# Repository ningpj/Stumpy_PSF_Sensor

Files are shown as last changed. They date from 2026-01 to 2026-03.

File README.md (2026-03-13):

# "_Stumpy_" Proportional Sync-Feedback (PSF) Sensor Enclosure for Multi Material Printing

During extended periods of synchronised printing without intervening tool changes, alignment between extruder and gear steppers can gradually drift. Even with precise calibration, factors such as under extrusion during purging, printing at high speed near upper flow limits, friction and drag and the inertia of heavy spools can conspire to cause slippage in either the extruder or more commonly—the downstream gear stepper. Over time, this mismatch accumulates and can lead to print artefacts caused by missed steps or suboptimal extrusion rates. Although not always apparent on well-tuned systems, it's a legitimate and demonstrable issue.

Proportional sync-feedback sensors address this using linear Hall Effect sensors (or similar), providing real-time analog positional telemetry to Happy-Hare allowing it to continuously adjust and fine tune the following gear stepper's Rotational Distance (`RD`).

This enclosure has been based around the excellent `PSF v1.0 / 1.1` Proportional Sync-Feedback sensor kit from [**Kashine6**](https://github.com/kashine6/Proportional-Sync-Feedback-Sensor?tab=readme-ov-file) (Discord: @jacksky6) and is intended to be used with the **Happy-Hare** MMU ecosystem and new Flowguard / Sync-feedback controller facilities (Happy-Hare `3.4.2` or later). `14.5 mm` of buffer range and works with `20 mm` or `25 mm` compression springs from the kit (`20 mm` preferred).

## References & Acknowledgements

This design has been completely reworked from the ground up, incorporating improvements informed by field testing of MK I and the earlier adaptation of [Tshine's original dual micro-switch based Sync-feedback Sensor](https://makerworld.com/en/models/507573) by [Kashine6](https://github.com/kashine6/Proportional-Sync-Feedback-Sensor?tab=readme-ov-file) to support Proportional Sync-Feedback sensors.

The primary goals have been to further reduce the overall form factor, optimise sensor–magnet alignment and constrain shuttle lateral movement to maximise Hall Affect ADC signal fidelity, particularly for top‑mounted MMUs and central Bowden entry ports. The assembly now measures just `63 mm` in length — `9.2 mm` shorter than Kashine6’s version and `3 mm` shorter than MK I revision. The `ECAS04` captive retention design has also been refined to make it easier to install them, hopefully without splitting the base. Printable `ECAS04` clips have also been included to colour coordinate ;-)  

## Assembly

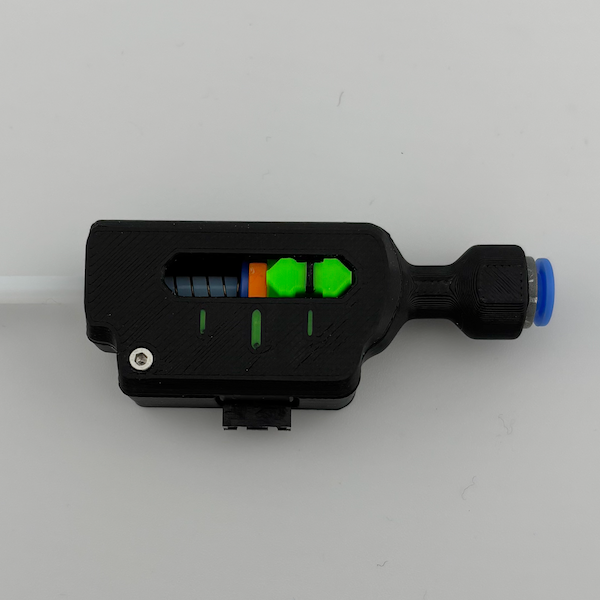
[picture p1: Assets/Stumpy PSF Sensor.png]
Stumpy PSF Sensor


> [!NOTE] 
> Step files (rather than STLs) are included for printing the sensor with [Multi-colour](MK%20II%20(Full%20redesign)/Multi_Colour_Step) tick marks or [Single-colour](MK%20II%20(Full%20redesign)/Single_Colour_Step) with recessed tick marks. Also consider lowering your 1st layer speed as the coloured elements are reasonably narrow to ensure tick marks are crisp and clean. 
> Depending on MMU / printer orientation, you may also consider inverting all parts (mirror along x axis in your slicer) to relocate the connector to the bottom of the unit to optimise wiring for your particular mmu setup.

Assembly is reasonably straight forward:

- Straighten the end of the PTFE tube you plan to use between the MMU and “Stumpy” PSF sensor. Avoid using PTFE with an `ID = 3.0 mm`. It klinks too easily especially if it needs to bend to accomodate the full range of gates / lanes which will jam the shuttle rather than moving freely for all selected gates.
- Check the body `4 mm` PTFE path with the PTFE tube to make sure its smooth and doesn't bind. Use a 4mm drill to gently remove any residual print artefacts around the 4 mm - 2 mm step down chamfer - Be careful not to damage the chamfer though.
- Install the `ECAS04` fittings without the optional rubber boot. You still need the hard plastic clasp cover on the base though.
- Press the `D4 × 15 mm` magnet into the PSF shuttle until it sits flush with the end opposite the `ECAS04` fitting. Magnet orientation doesn’t matter; Happy-Hare will calibrate it.
- Insert the  `2.0 – 2.5 mm ID` PTFE feeder tube from the left, feeding it through the `20 mm` spring (or `25 mm` if this is all you have) and shuttle until it bottoms out in the body recess. Adjust so it neither binds nor pulls out when held against the opposite stop. Install the colour coordinated `ECAS04` clip with the 90° top facing the shuttle so it’s retained and prevented from rotating by the nubs provided.
- Insert the `PSF 1.0 / v1.1` PCB module into the provided slot.
- Slide the lid / cover on from the back over the shuttle and onto the base, aligning the parts and snapping them gently onto the locating nubs. Do not force it. Secure with a single `M2 × 6 mm SHCS`.
- Confirm the shuttle moves freely across its full travel before installing.

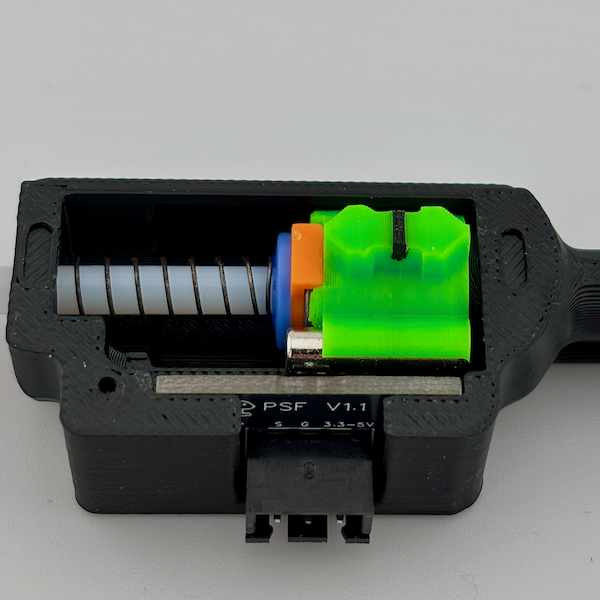
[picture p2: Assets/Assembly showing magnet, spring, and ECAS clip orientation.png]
Assembly showing magnet ECSA clip positions


## Bill of Materials (BOM)

| Item | Specification | Quantity |
| --- | --- | --- |
| **PSF v1.0/1.1+ Board** | Inexpensive kit from [Aliexpress](https://www.aliexpress.com/item/1005010470743517.html) that includes all the required parts below | 1 |
| **Spring** | 0.4 mm × 6 mm × 20 mm, spring steel ( If longer, e,g 25mm, cut down and shorten it, tiding up the cut end with needle nose pliers | 1 |
| **Magnet** | D4 mm × 15 mm N35 | 1 |
| **ECAS04 Bowden connector & clips**| | 2 |
| **M2×6 mm SHCS screw** | | 1 |
| **PTFE feeder tube** | Short PTFE feeder tube installed between the “Stumpy” PSF Sensor and the MMU (2.5 mm ID recommended) - 3 mm ID PTFE tube is too flexible and will deform or jam if its bent too much. | |

## Prerequsites

"Stumpy" PSF needs to be used inconjunction with `Happy-Hare` Flowguard **integrated** support for Proportional Feedback Sensors (Release `3.4.2` or later). Please refer to https://github.com/moggieuk/Happy-Hare/wiki/Synchronized-Gear-Extruder2 for proportional sensor setup, configuration, and usage instructions.

## Happy-Hare Configuration

`MMU_PARAMETERS.CFG`

The "Stumpy" PSF Sync-Feedback Sensor has 14.5mm of buffer / sensor range.

```yaml
sync_feedback_buffer_range: 14.5 		# Travel in "buffer" between compression/tension or one sensor and end (see above)
sync_feedback_buffer_maxrange: 14.5 	# Absolute maximum end-to-end travel (mm) provided by buffer (see above)
```

In `MMU_HARDWARE.CFG` set `sync_feedback_analog_pin: mmu:<ADC GPIO>` to a valid analog-capable GPIO port on the MCU you connected the "Stumpy" PSF sensor to. If `sync_feedback_*` parameters aren't defined under your `[mmu_sensor]` section, insert the following block manually, setting `compression`, `tension`, and `neutral_point` to 1, 0, & 0.5 respectively. 

[Kashine6](https://github.com/kashine6/Proportional-Sync-Feedback-Sensor?tab=readme-ov-file) provides a breakdown on their GITHUB of valid ADC GPIO ports for many popular MMU MCU's.  Note that while many boards offer multiple ADC-capable GPIO's, only one port has been fully verified and documented for each board.

Restart Klipper, load a gate with filament and run `MMU_CALIBRATE_PSENSOR` to determine the minimum and maximum ADC values returned by your PSF v1.0 / v1.1 Sensor module. Use these values to configure the corresponding parameters in `MMU_HARDWARE.CFG`. Your sensor may produce different or inverted—readings compared to the example below. This is expected, and Happy-Hare can accommodate it.

```yaml
sync_feedback_analog_pin: mmu:<Your analog-capable GPIO> # The ADC pin where the proportional filament pressure sensor is installed
sync_feedback_analog_max_compression: 0.9964             # Raw sensor reading at max filament compression (buffer squeezed)
sync_feedback_analog_max_tension: 0.0046                 # Raw sensor reading at max filament tension (buffer expanded)
sync_feedback_analog_neutral_point: 0.5005               # Sensor neutral point (tunable to apply positive tension on the filament to unburden the Bowden and extruder)
```

## Installation Options

Normal orientation with connector on top for right hand installation. Optionally mirror parts along x axis in your slicer to relocate the connector to the bottom of the unit to optimise wiring / visibility for your particular mmu setup.

For setups with a central PTFE entry port like mine, consider installing a PTFE guide as shown below to help straighten the PTFE path and ensure the sensor shuttle moves freely no matter the gate selected [Makerworld: HamAndChris 90°, 180°, or 60° PTFE Bowden tube bend guide](https://makerworld.com/en/models/1033408-90deg-180deg-or-60deg-ptfe-bowden-tube-bend-guide#profileId-1016713).

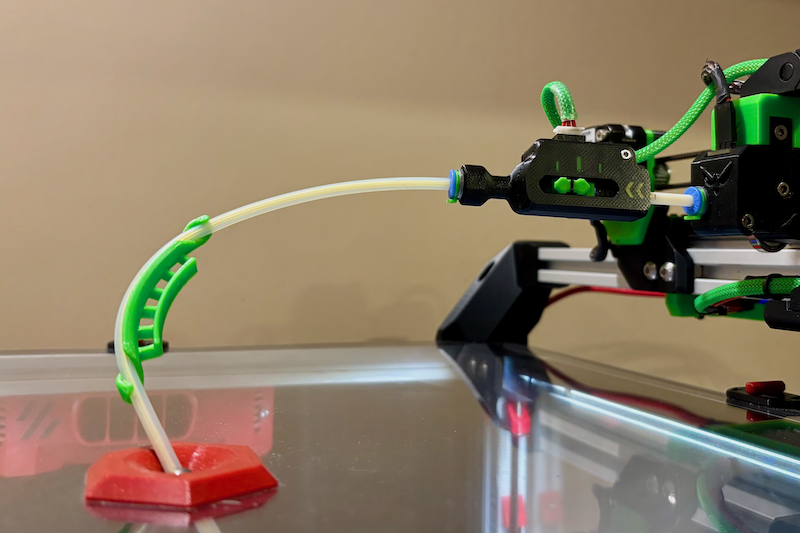
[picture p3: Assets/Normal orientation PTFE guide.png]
Normal Orientation, wired from top with PTFE guide
 

## Optional Shuttle with 3x2mm Magnet Stack

This variant is intended for people who want to self‑source / build the PSF sensor and have difficulty obtaining the preferred D4×15 mm magnet. Instead, it uses a stack of commonly available 3×2-ish mm N35 magnets. Depending on their thickness, the carrier will accept a stack of 7–9 magnets. When installing the shuttle ECAS, take care not to crack or deform the carrier.

Because magnetic flux varies, you may need to adjust the stack height or shift its position slightly to achieve saturation of the Hall‑effect sensor at both travel extremes. This tuning step is optional—the sensor will still function reliably without it. In testing, for example, saturation was achieved with eight magnets and the stack offset approximately 1.5 mm from the right side of the shuttle.

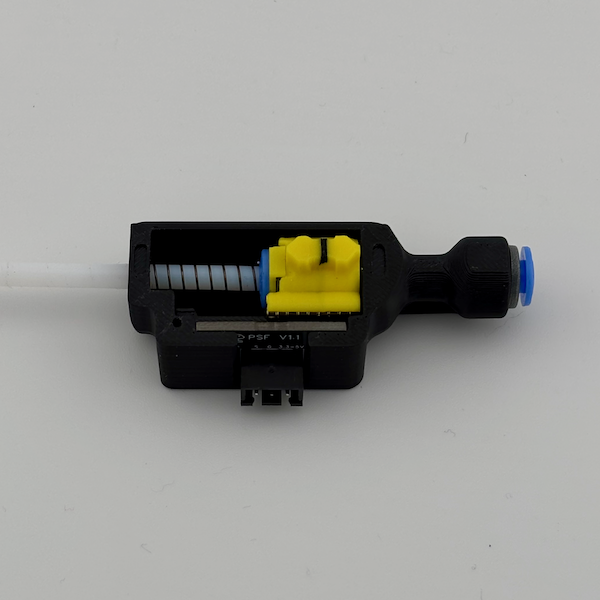
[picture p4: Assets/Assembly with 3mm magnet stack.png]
Optional 3x2mm Magnet Stack

<br>
<br>
With the slightly offset 3x2mm magnet stack (8), excellent `MMU_CALIBRATE_PSENSOR` results were achieved by repeatly adjusting the position / number of magnets and rerunning `MMU_CALIBRATE_PSENSOR` to confirm results.  

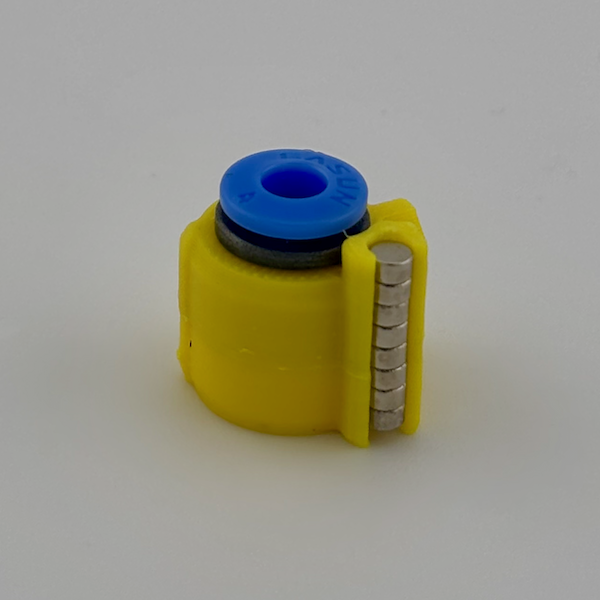
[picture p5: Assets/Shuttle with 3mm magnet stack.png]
Optimal 3x2mm Magnet offset


```yaml
// sync_feedback_analog_max_compression: 0.9809
// sync_feedback_analog_max_tension:     0.0043
// sync_feedback_analog_neutral_point:   0.4926
```

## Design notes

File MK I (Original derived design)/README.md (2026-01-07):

# *"Stumpy"* Proprotional Sync-Feedback (PSF) Sensor for Multi Material Printing

During extended periods of synchronised printing without intervening tool changes, alignment between extruder and gear steppers can gradually drift. Even with precise calibration, factors such as under extrusion during purging, printing at high speed near upper flow limits, friction and drag and the inertia of heavy spools can conspire to cause slippage in either the extruder or more commonly—the downstream gear stepper. Over time, this mismatch accumulates and can lead to print artefacts caused by missed steps or suboptimal extrusion rates. Although not always apparent on well-tuned systems, it's a legitimate and demonstrable issue.

Proportional sync-feedback sensors address this using linear Hall Effect sensors (or similar), providing analog positional telemetry to Happy Hare allowing it to continuously adjust and fine tune gear stepper Rotational Distance (RD).

This redesign is based around the PSF v1.0/1.1 or later proportional sensor kit from **Kashine6** on ALiexpress and is intended to be used with the **Happy Hare** MMU ecosystem and new Flowguard / Sync-feedback controller.

## References & Acknowledgements

This design is based on the original works of [Tshine's Dual Micro-switch based Sync-feedback Sensor](https://makerworld.com/en/models/507573) and subsequent adaption to accomodate Proportional Sync-Feedback (PSF) sensor circuitry and magnet by [Kashine6](https://github.com/kashine6/Proportional-Sync-Feedback-Sensor?tab=readme-ov-file). Its been optimised (sensor / magnet placement, mainbody changes, etc) and significantly shortened (65mm - 6.2mm shorter than Kashine6's version) to work better with top mounted MMU's and bowden entry ports.

## Assembly

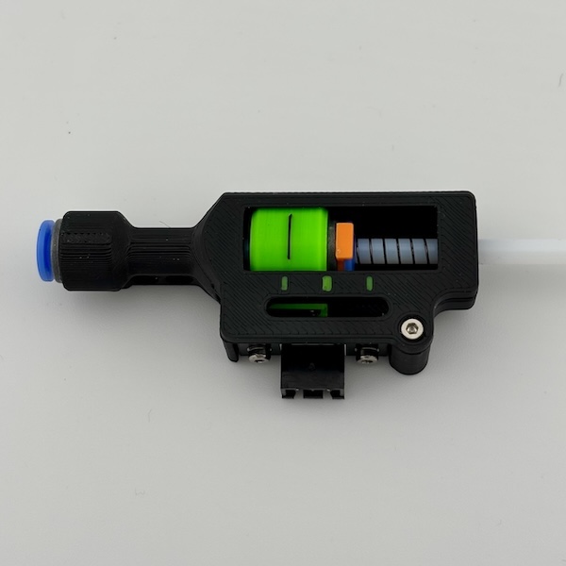
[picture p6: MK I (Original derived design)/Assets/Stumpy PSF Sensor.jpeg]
Stumpy PSF Sensor


> [!NOTE] 
> Step files (rather than STLs) are included for printing the sensor with [Multi-colour](Multi_Colour_Step) tick marks or  [Single-colour](Single_Colour_Step) with recessed tick marks.
> Depending on MMU / Printer orientation, you may elect to invert all the parts (mirror along x axis in your slicer) to move the connector to the top to streamline wiring. 

Assembly is reasonably straight forward.

- Install ECAS fittings without rubber boots
- Install D4 x 15mm magnet in PSF shuttle until it's flush with the end of the shuttle (magnetic orientation doesn't matter)
- Straighten the PTFE tube you will be inserting into the "Stumpy" PSF body
- Insert the PTFE tube from the right, threading through the spring and PSF shuttle until it bottoms out on the recess of the body. Install the ECAS clip to secure
- Hold the shuttle up against the stop on the left hand side of the body. Using a small screw driver or hex key, push and adjust the magnet until it bottoms out in the recess for it on the body. Once in position, it should sit proud of the PSF shuttle by 4mm as per the image below
- Use 2 M2 x 6mm SHCS screws to install the PSF module
- Use a M2 x 6mm SHCS screw to secure the cover
- Verify the shuttle moves freely across its full range of movement

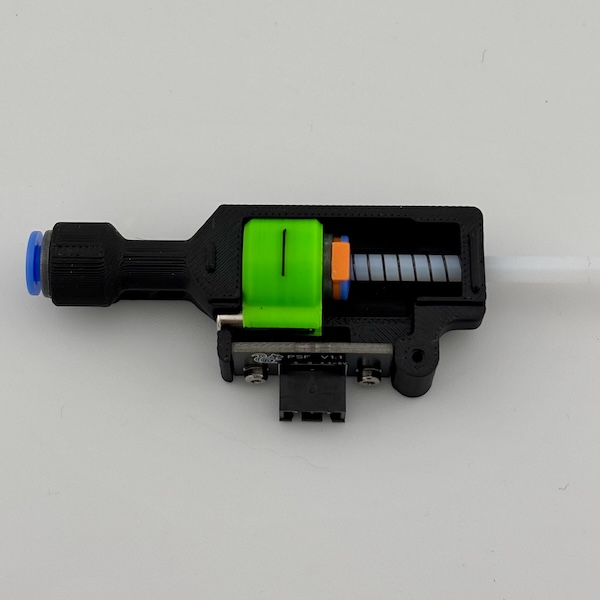
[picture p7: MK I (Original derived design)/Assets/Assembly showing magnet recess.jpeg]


## Bill of Materials (BOM)

| Item | Specification | Quantity |
| --- | --- | --- |
| **PSF v1.1+ Board** | Kit from [Aliexpress](https://www.aliexpress.com/item/1005010470743517.html) includes all the required parts below | 1 |
| **Spring** | 0.4 mm × 6 mm × 20 mm, spring steel (cut down and shorten kit spring if too long | 1 |
| **Magnet** | D4 mm × 15 mm N35 | 1 |
| **ECAS04 Bowden connector & clips**| | 2 |
| **M2×6 mm SHCS screw** | | 3 |

## Prerequsites

This needs to be used with `Happy Hare` Flowguard and **integrated** support for Proportional Feedback Sensors.
Please refer to https://github.com/moggieuk/Happy-Hare/wiki/Synchronized-Gear-Extruder2 for detailed setup and configuration instructions.

> [!NOTE] 
> You will need to switch to the Happy Hare `FLOWGUARD` branch before configuring the sensor until the `beta` is complete and merged with the main Happy Hare release.  
>
> ```text
> cd ~/Happy-Hare
> ./install.sh -b FLOWGUARD
> ```

## Happy Hare Configuration

`MMU_PARAMETERS.CFG`

The "Stumpy" PSF Sync-Feedback Sensor has 14mm of movement.

```yaml
sync_feedback_buffer_range: 14 		# Travel in "buffer" between compression/tension or one sensor and end (see above)
sync_feedback_buffer_maxrange: 14 	# Absolute maximum end-to-end travel (mm) provided by buffer (see above)
```

Use `MMU_CALIBRATE_PSENSOR` to determine the min and max ADC raw values returned by the sensor to set the following parameters in `MMU_HARDWARE.CFG`. Your sensor may return different values than the example below e.g.:

```yaml
sync_feedback_analog_pin: mmu:<ADC GPIO>          # The ADC pin where the proportional filament pressure sensor is installed
sync_feedback_analog_max_compression: 0.0038      # Raw sensor reading at max filament compression (buffer squeezed)
sync_feedback_analog_max_tension: 0.9919          # Raw sensor reading at max filament tension (buffer expanded)
sync_feedback_analog_neutral_point: 0.4979        # Neutral point
```

## Installation Options

Normal orientation (as designed)

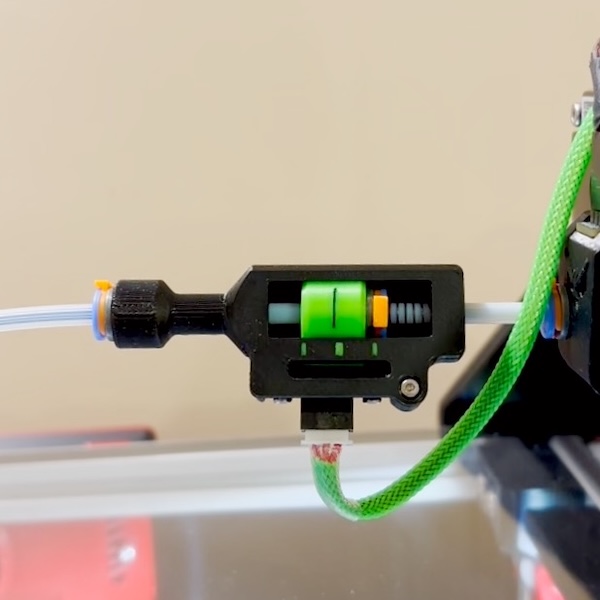
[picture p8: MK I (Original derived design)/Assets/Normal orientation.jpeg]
Normal Oriented (As designed)


**[Optional]** Inverted (Mirror all parts along x axis in your slicer)

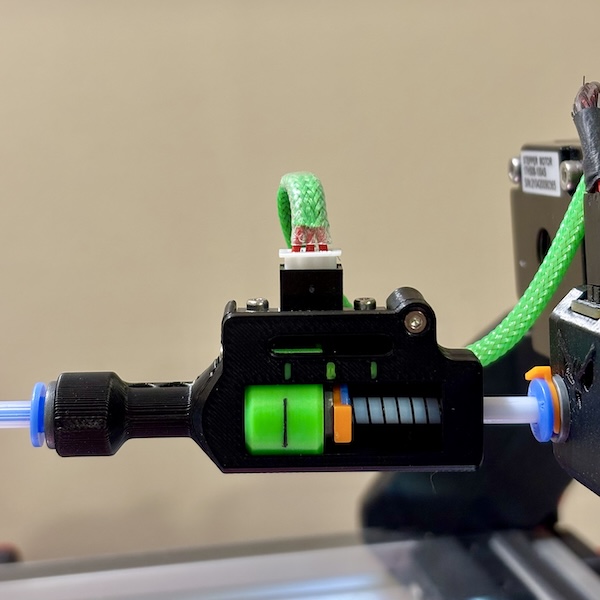
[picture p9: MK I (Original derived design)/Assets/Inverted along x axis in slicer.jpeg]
Inverted Orientation


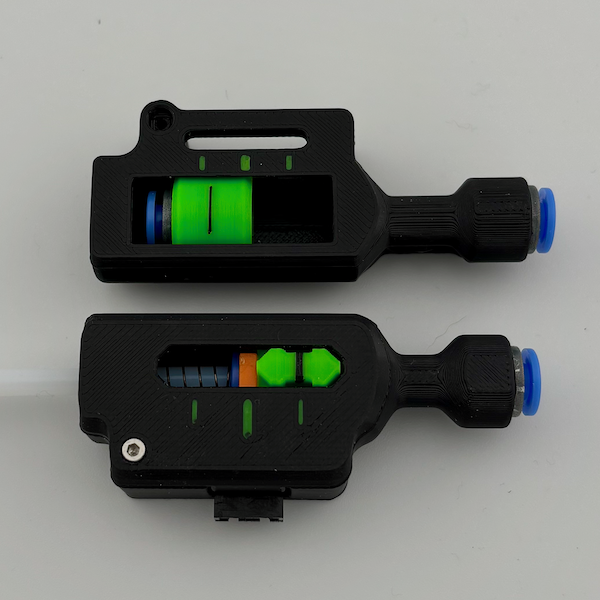
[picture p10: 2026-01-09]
Assets/MK I & II comparison.png

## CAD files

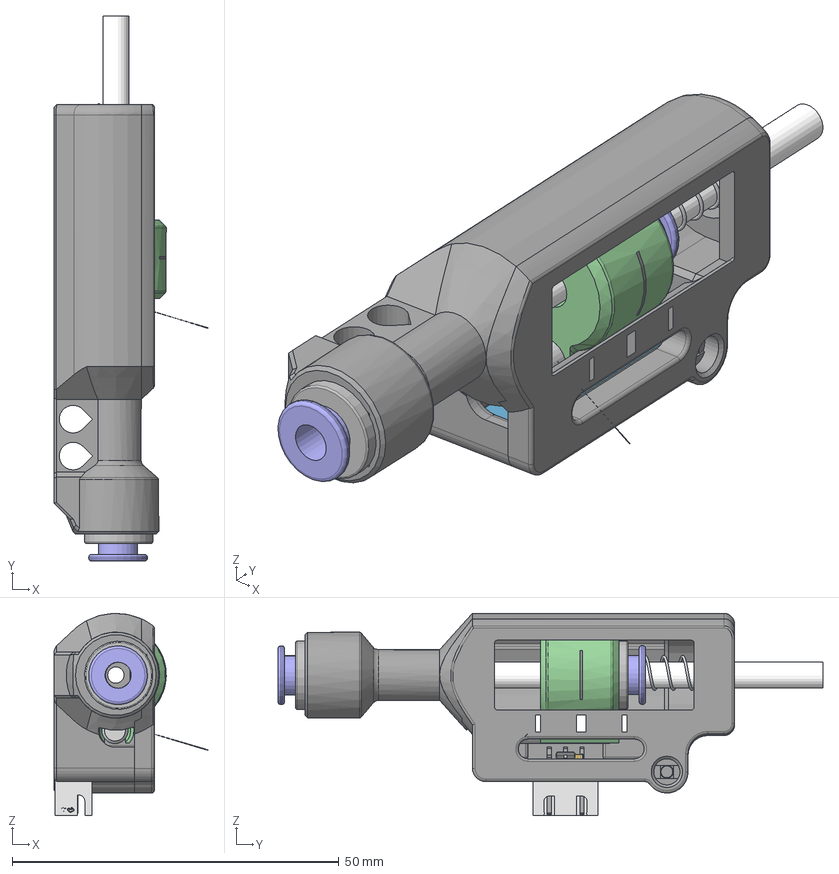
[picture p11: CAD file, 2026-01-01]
MK I (Original derived design)/CAD/Stumpy_PFS_Single_Spring_Clean v2.step
23.5 x 83.3 x 30.9 mm
sensor_housing
sensor_housing_1
slider
Magnet_D4x15
MAuh-Board
MAuh-U1-SOT-23-3_L2.9-W1.6-P1.90-LS2.8-BR-CW
MAuh-C1-C0603
ECAS Fitting v1 x 2
PTFE
Spring_0.4x5x25

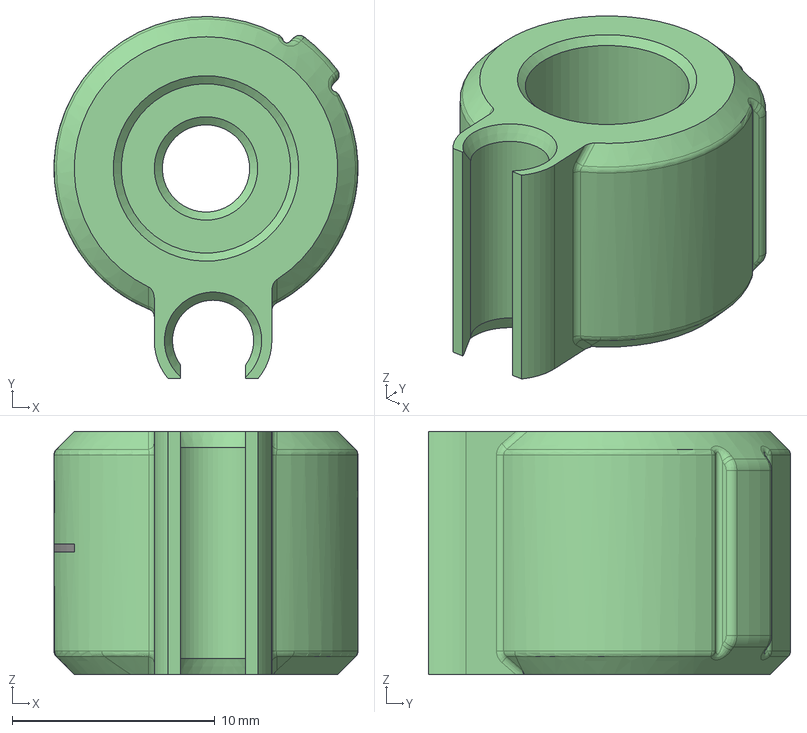
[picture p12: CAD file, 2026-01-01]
MK I (Original derived design)/Multi_Colour_Step/Stumpy_PSF_Shuttle 12mm v2.step
15.0 x 17.9 x 12.0 mm

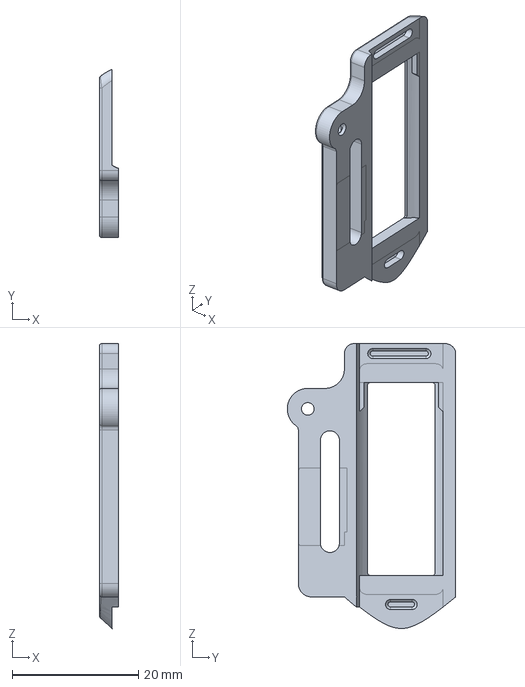
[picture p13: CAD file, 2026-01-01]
MK I (Original derived design)/Single_Colour_Step/Stumpy_PSF_Cover v2.step
3.04 x 26.7 x 45.1 mm

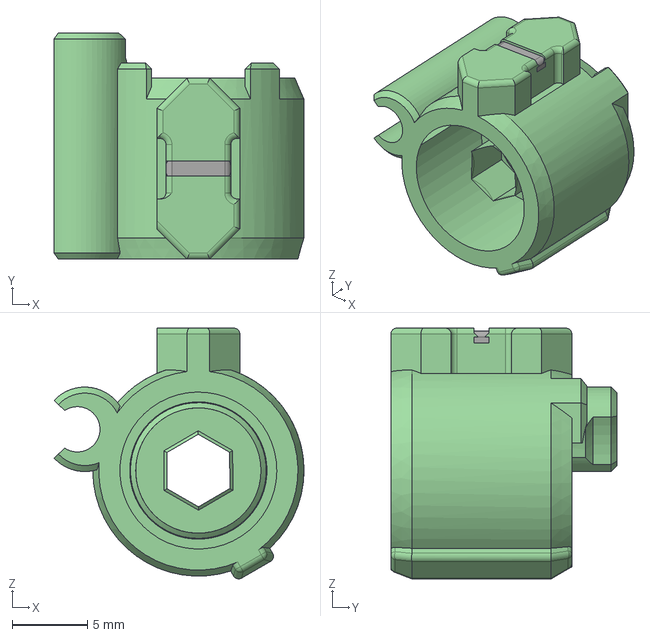
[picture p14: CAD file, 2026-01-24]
MK II (Full redesign)/Multi_Colour_Step/3x2mm magnet stack option/Stumpy PSF MK II Shuttle 3x2 magnet stack.step
16.6 x 15.0 x 16.6 mm

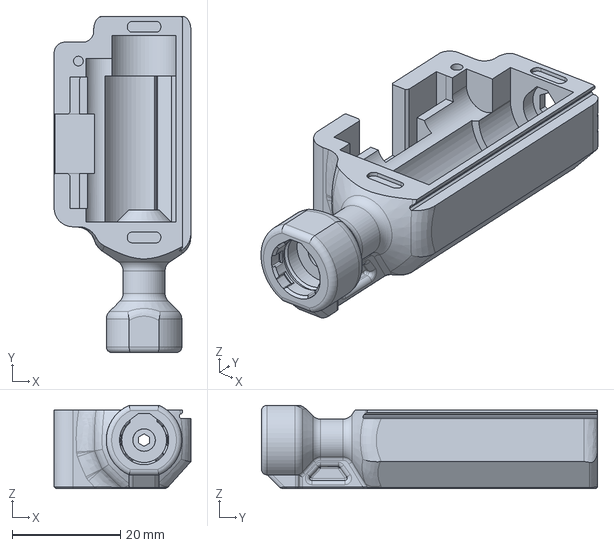
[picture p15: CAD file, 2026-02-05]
MK II (Full redesign)/Multi_Colour_Step/Stumpy PSF MK II Case.step
25.3 x 62.2 x 15.4 mm

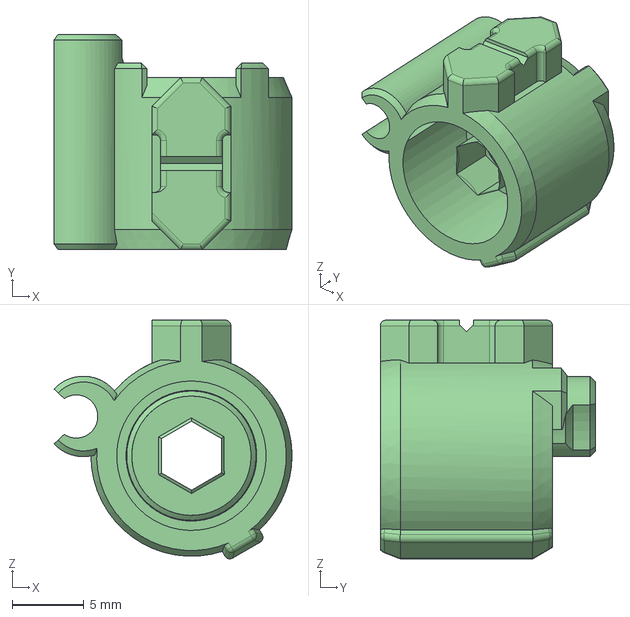
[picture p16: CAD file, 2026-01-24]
MK II (Full redesign)/Single_Colour_Step/3x2mm magnet stack option/Stumpy PSF MK II Shuttle 3x2 magnet stack.step
16.6 x 15.0 x 16.6 mm

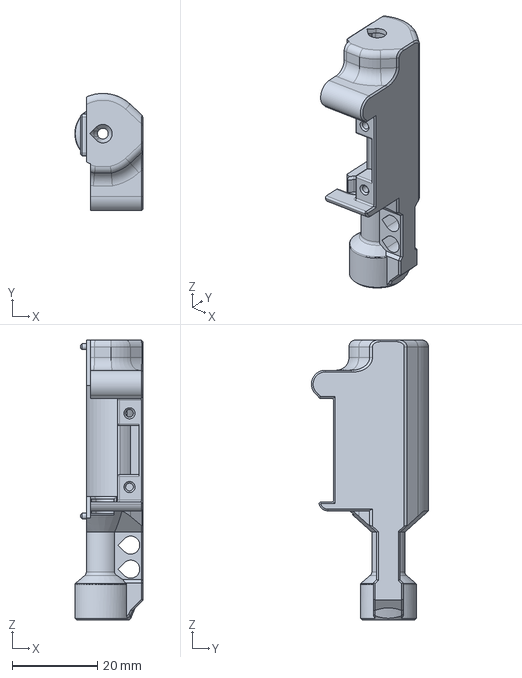
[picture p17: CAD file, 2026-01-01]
MK I (Original derived design)/Multi_Colour_Step/Stumpy_PSF_Housing v2.step
16.0 x 27.5 x 65.7 mm

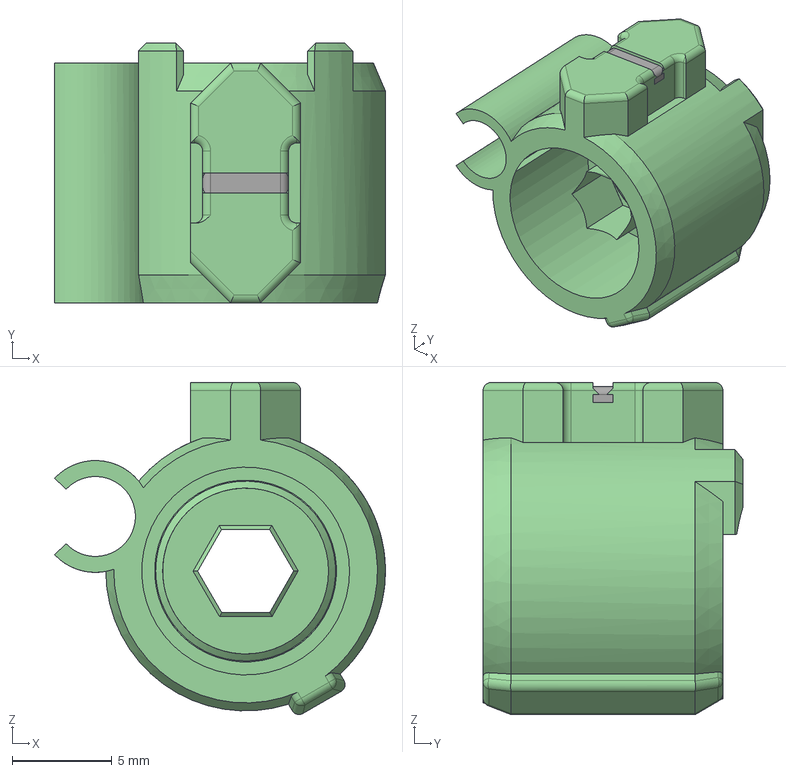
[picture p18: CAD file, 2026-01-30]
MK II (Full redesign)/Multi_Colour_Step/Stumpy PSF MK II Shuttle.step
16.6 x 13.0 x 16.6 mm

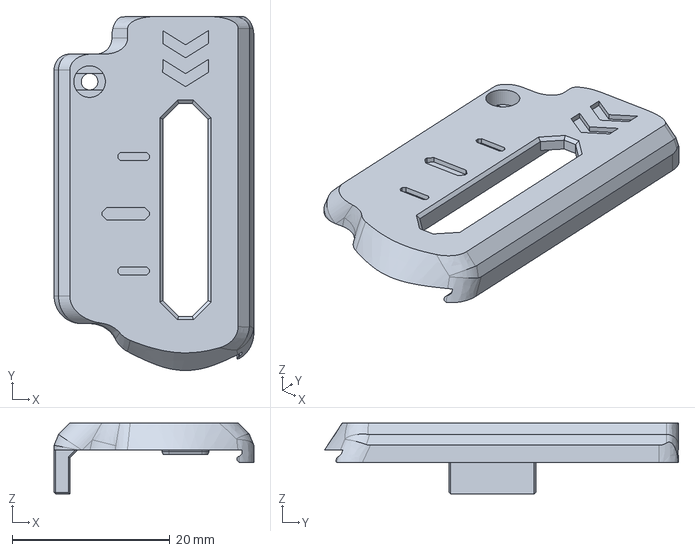
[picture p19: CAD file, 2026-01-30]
MK II (Full redesign)/Single_Colour_Step/Stumpy PSF MK II Lid.step
25.3 x 44.9 x 8.97 mm

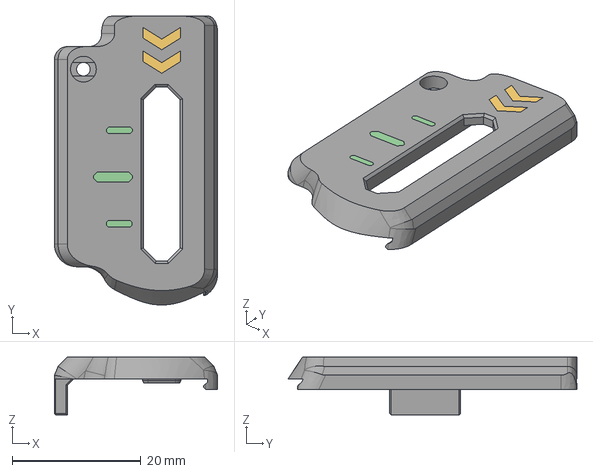
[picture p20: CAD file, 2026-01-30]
MK II (Full redesign)/Multi_Colour_Step/Stumpy PSF MK II Lid.step
25.3 x 44.9 x 8.97 mm

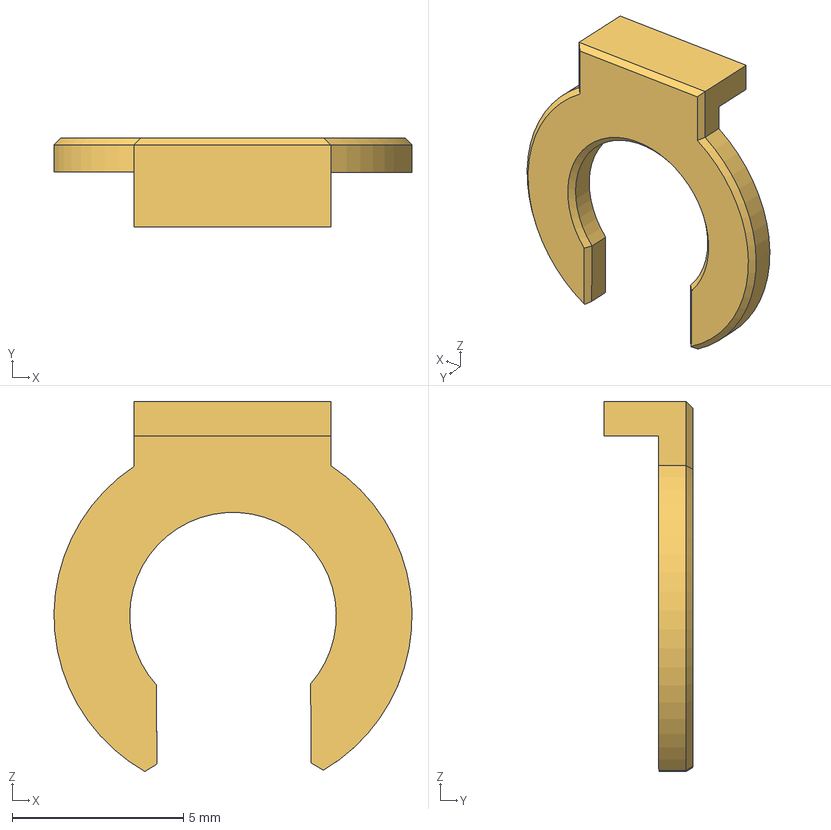
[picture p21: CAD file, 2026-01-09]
MK II (Full redesign)/Multi_Colour_Step/Stumpy PSF MK II Printable ECAS Clip (2x).step
10.4 x 2.60 x 10.8 mm

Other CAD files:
MK II (Full redesign)/Single_Colour_Step/Stumpy PSF MK II Case.step
MK I (Original derived design)/Single_Colour_Step/Stumpy_PSF_Housing v2.step
MK I (Original derived design)/Multi_Colour_Step/Stumpy_PSF_Cover v2.step
MK I (Original derived design)/Single_Colour_Step/Stumpy_PSF_Shuttle 12mm v2.step
MK II (Full redesign)/Single_Colour_Step/Stumpy PSF MK II Shuttle.step
MK II (Full redesign)/Single_Colour_Step/Stumpy PSF MK II Printable ECAS Clip (2x).step

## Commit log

2026-01-01 Create README.md
    Added detailed information about the Stumpy PSF Sync-Feedback Sensor, including its purpose, references, bill of materials, and configuration instructions.
2026-01-02 Refine assembly instructions in README.md
    Clarify instructions for inserting PTFE tube and adjusting magnet position.
2026-01-02 Revise references and optimize design description
    Updated reference to Tshine's sensor and added optimization note.
2026-01-02 Update README with assembly note on part orientation
    Added note about inverting parts for connector placement.
2026-01-02 Update README with image reference for magnet adjustment
    Clarified instructions for magnet positioning in PSF shuttle.
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2026-01-07 MK II Full Redesign
    Shorter, fully enclosed, ground up redesign
    [Stumpy PSF MK II Case.step, Stumpy PSF MK II Lid.step, Stumpy PSF MK II Shuttle.step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]
2026-01-07 Rearrance files
    [Stumpy PSF MK II Case.step, Stumpy PSF MK II Lid.step, Stumpy PSF MK II Shuttle.step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]
2026-01-07 Rearrange files
    [Stumpy PSF MK II Case.step, Stumpy PSF MK II Lid.step, Stumpy PSF MK II Shuttle.step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]
2026-01-07 Publish MK II WIP steps & rearrange dir structure
    [Stumpy PSF MK II Case.step, Stumpy PSF MK II Lid.step, Stumpy PSF MK II Shuttle.step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]
2026-01-07 Revise README for PSF sensor redesign details
    Updated the README to reflect the redesign of the Proportional Sync-Feedback sensor kit, including changes to specifications and warnings about the work in progress.
2026-01-07 Clarify sync-feedback sensor functionality in README
    Clarify the description of the proportional sync-feedback sensors by specifying that they fine-tune the following gear stepper's Rotational Distance.
2026-01-07 Update README with sensor kit version and design details
    Clarified the versioning of the proportional sensor kit and improved the description of design optimizations.
2026-01-07 Update README with design improvements and assembly notes
    Improved clarity on design changes and assembly instructions.
2026-01-08 Drop mmu colour tick down one layer to improve edge quality
    [Stumpy PSF MK II Shuttle.step]
2026-01-08 Update full cad
    [Stumpy PSF MKII v169.step, Stumpy PSF MKII v171.step]
2026-01-08 Update Stumpy PSF MK II Shuttle.step
    [Stumpy PSF MK II Shuttle.step]
2026-01-08 Cleanup steps
    [Stumpy PSF MK II Shuttle.step, Stumpy PSF MKII v171.step, Stumpy PSF MKII v173.step]
2026-01-08 Refine ticks to improve printability
    [Stumpy PSF MK II Lid.iges, Stumpy PSF MKII v173.step]
2026-01-08 Fixes - missing extruded face
    [Stumpy PSF MK II Case.step, Stumpy PSF MK II Lid.iges, Stumpy PSF MK II Lid.step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]
2026-01-08 Tweaks to improve printability
    [Stumpy PSF MK II Lid.step, Stumpy PSF MKII v179.step, Stumpy PSF MKII v181.step]
2026-01-08 Updated images, instructions, ease PSF slot
    [Stumpy PSF MK II Case.step, Stumpy PSF MKII v181.step, Stumpy PSF MKII v182.step]
2026-01-08 Add ECAS clip retainer to shuttle
    [Stumpy PSF MK II Shuttle.step, Stumpy PSF MKII v182.step, Stumpy PSF MKII v185.step]
2026-01-08 Reduce depth of PSF sensor pocket
    It "should" sit flush with top of case
    [Stumpy PSF MK II Lid.step, Stumpy PSF MKII v185.step]
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2026-01-08 Micro clearance adjustments
    [Stumpy PSF MK II Case.step]
2026-01-08 Tweaking clearances
    [Stumpy PSF MKII v189.step]
2026-01-08 Restructure directories
    [Stumpy_PFS_Single_Spring_Clean v2.step, Stumpy_PSF_Cover v2.step, Stumpy_PSF_Housing v2.step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]
2026-01-08 Fix typo in MMU wiring instructions
    Corrected a typo in the README regarding MMU orientation.
2026-01-09 Printable ECAS, arrows & revert to hex filament path
    [Stumpy PSF MK II Case.step, Stumpy PSF MK II Lid.step, Stumpy PSF MK II Printable ECAS Clip (2x).step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]
2026-01-09 Confirmed 14.5mm full movement range, move marker ticks accordingly
    [Stumpy PSF MK II Lid.step]
2026-01-09 Cleanup release
    [Stumpy_PSF_Cover v2.step, Stumpy_PSF_Housing v2.step, Stumpy_PSF_Shuttle 12mm v2.step]
2026-01-09 Widen tick marks to make more distinct
    [Stumpy PSF MK II Lid.step]
2026-01-11 Move sensor to minimise dead zones at compression extreme
    [Stumpy PSF MK II Case.step, Stumpy PSF MK II Lid.step]
2026-01-11 Add step to check and clean the PTFE path with a 4mm drill if necessary
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2026-01-20 3x2mm magent stack option (beta)
    [Stumpy PSF MK II Shuttle 3x2 magnet stack.step]
2026-01-21 3x2 magnet stack option (beta)
    [Stumpy PSF MK II Shuttle 3x2 magnet stack.step]
2026-01-24 Clearance for ECAS clip
    [Stumpy PSF MK II Shuttle 3x2 magnet stack.step]
2026-01-24 Optional 3x2mm magnet stack updates
    Optional shuttle and support for 3x2mm N35 magnet stack instead of recommended D4 15mm magnet
    [Stumpy PSF MK II Shuttle 3x2 magnet stack.step]
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2026-01-25 Adjust shuttle / lid clearances
    [Stumpy PSF MK II Lid.step]
2026-01-30 Rotate PTFE hex channel to make it easier to print
    [Stumpy PSF MK II Case.step, Stumpy PSF MK II Lid.step, Stumpy PSF MK II Shuttle.step]
2026-02-02 Clarify installation options and magnet stack details
    Updated text for clarity and improved visibility regarding wiring options and magnet stack specifications.
2026-02-02 Improve clarity on MMU_CALIBRATE_PSENSOR results process
    Clarified the process for achieving excellent MMU_CALIBRATE_PSENSOR results by adjusting the position and number of magnets, and rerunning the calibration.
2026-02-03 Fix typo in README.md for calibration instructions
2026-02-05 Improve printability
    [Stumpy PSF MK II Case.step]
2026-02-21 Clarify PTFE feeder tube description in README
    Updated description of PTFE feeder tube to clarify that 3 mm ID tube is too flexible.
2026-03-04 Refactor README for clarity and remove duplicates
    Removed duplicate instructions and unnecessary note about switching branches.
2026-03-04 Update README with PSF sensor setup instructions
    Clarified instructions for setting up the PSF sensor in MMU_HARDWARE.CFG and added details on ADC values.
2026-03-06 Refine README.md for PSF sensor kit details
    Updated the description of the Proportional Sync-Feedback sensor kit for clarity and consistency.
2026-03-13 Revise title and description for PSF sensor enclosure
    Updated the title and description for clarity.
